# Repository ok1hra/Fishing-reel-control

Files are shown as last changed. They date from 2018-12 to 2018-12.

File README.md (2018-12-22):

# Fishing-reel-control 

KiCad PCB layout
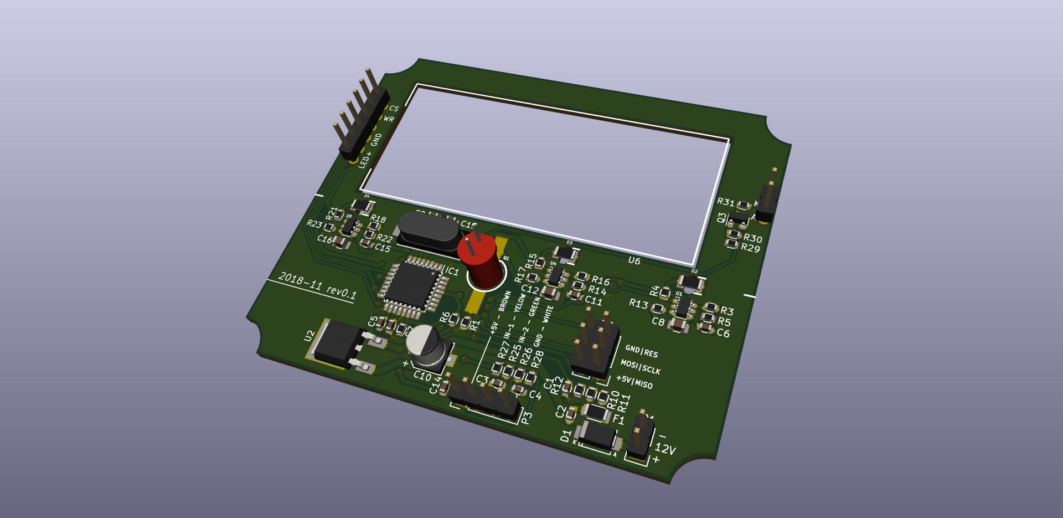
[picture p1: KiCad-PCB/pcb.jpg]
PCB


* [Schematics](KiCad-PCB/Ali-FM.pdf)
* [Interactive bom!](http://htmlpreview.github.io/?https://github.com/ok1hra/Fishing-reel-control/blob/master/KiCad-PCB/ibom.html)
* [STEP 3D model of PCB](KiCad-PCB/Ali-FM.step)
* [Firmware](https://github.com/ok1hra/Fishing-reel-control/tree/master/Arduino_firmware)

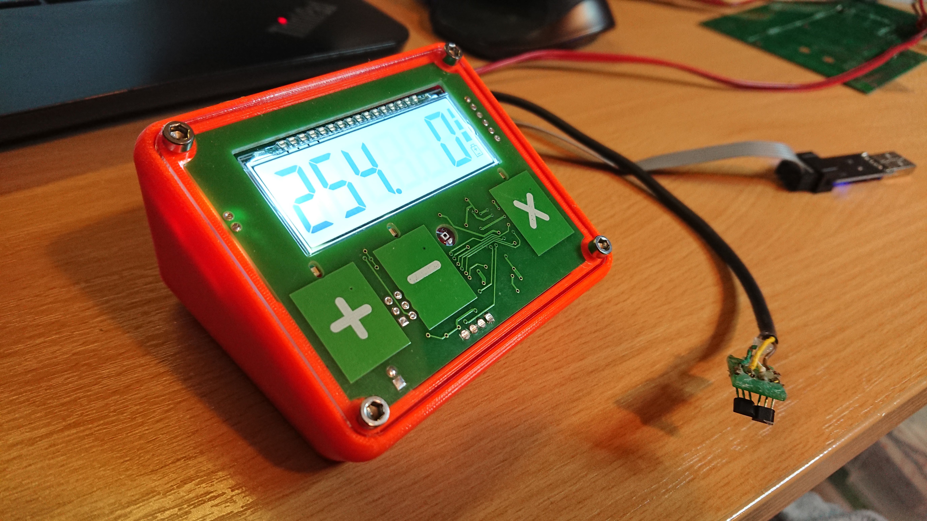
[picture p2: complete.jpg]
Complete


## Functionality
* Show battery voltage at start up
* LCD show counter, speed in metre unit + battery voltage bargraph
* Capacitive button sensor for up, down an reset with LED light feedback
* Ambient light sensor automaticaly adjust LCD backlight
* After 20 seconds storage last value, for recovery after restart power
* 12V DC power input
* Counter input for two hall effect switch
* Waterproof 3D printed case (PET)

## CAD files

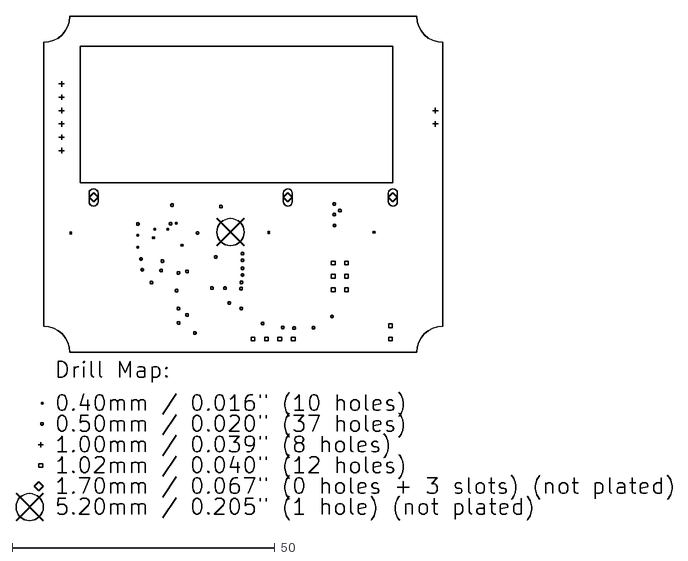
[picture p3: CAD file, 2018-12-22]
KiCad-PCB/gerber/Ali-FM-drl_map.dxf
124.9 x 96.1

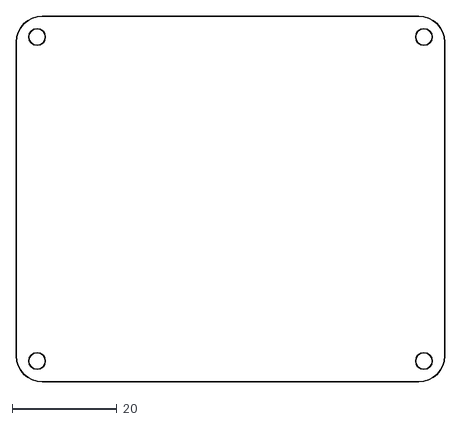
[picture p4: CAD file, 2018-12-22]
OpenScad-3Dmodel/plexi.dxf
82.0 x 70.0

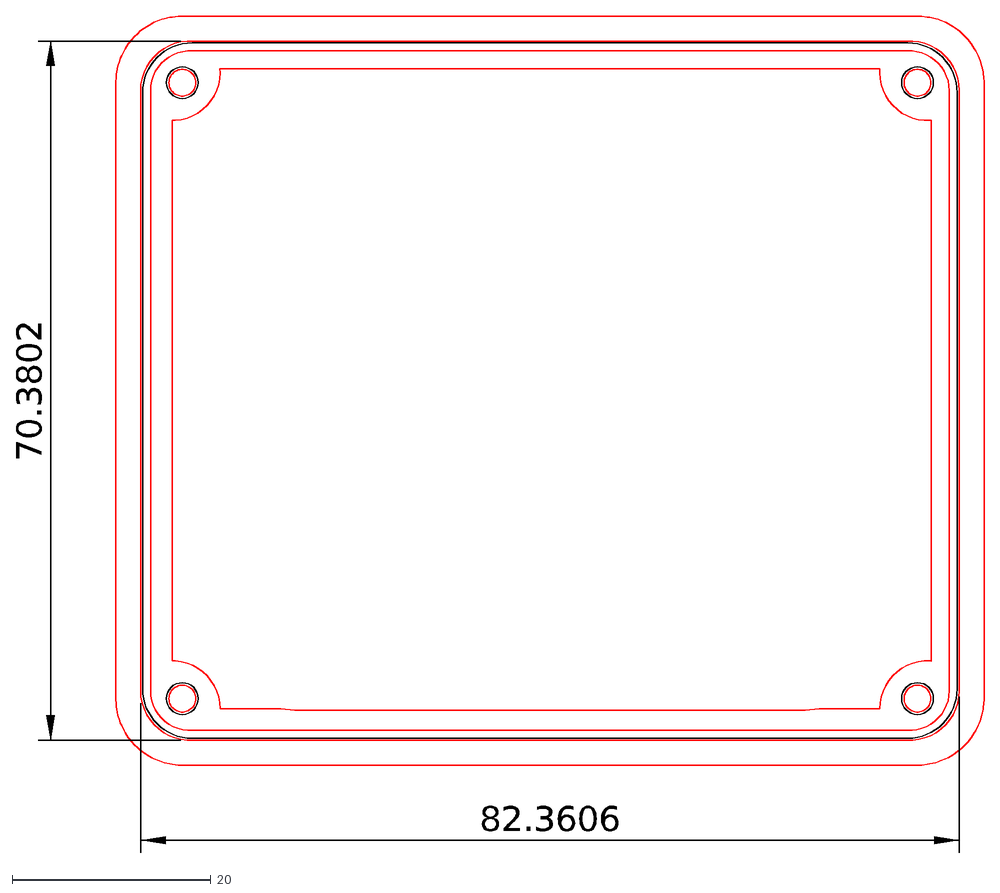
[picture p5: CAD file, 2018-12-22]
OpenScad-3Dmodel/ali-cut.dxf
70.3802
82.3606

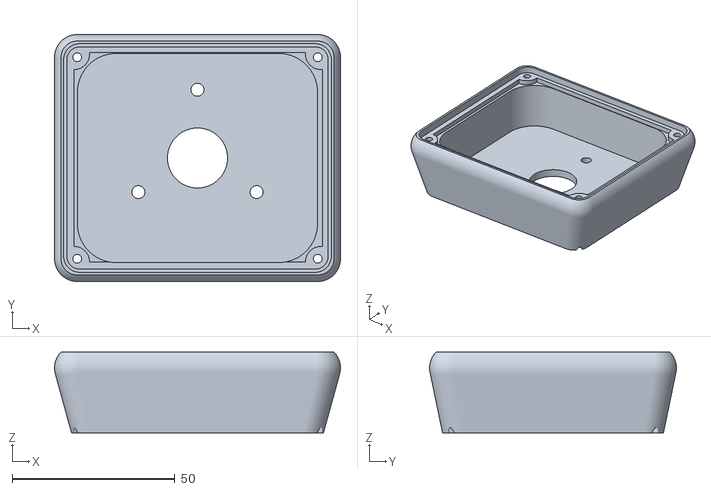
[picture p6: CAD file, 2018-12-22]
OpenScad-3Dmodel/ali.stl
88.0 x 76.0 x 24.9

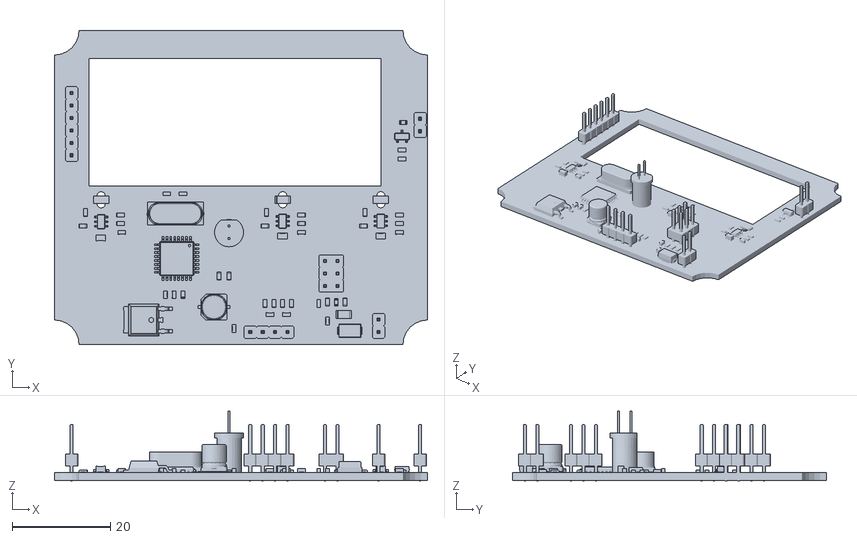
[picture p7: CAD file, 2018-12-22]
OpenScad-3Dmodel/Ali-FM.stl
76.0 x 64.0 x 14.2

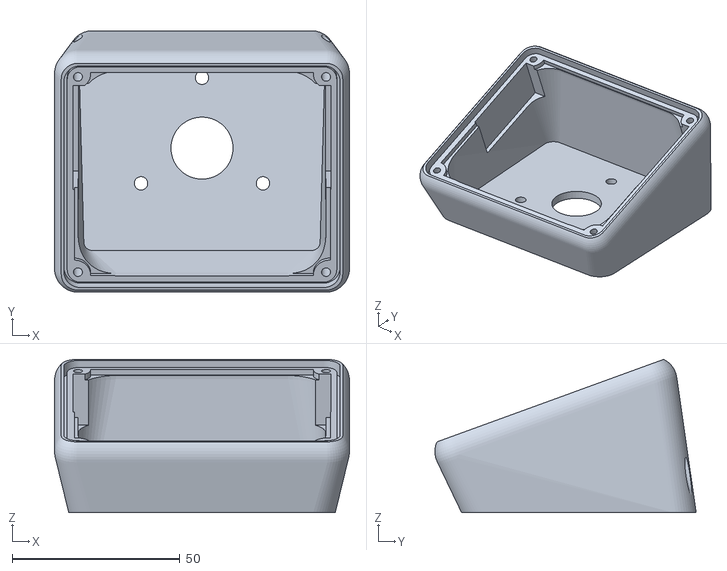
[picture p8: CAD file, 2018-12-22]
OpenScad-3Dmodel/ali2.stl
88.0 x 77.9 x 45.7

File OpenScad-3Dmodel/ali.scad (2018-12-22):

$fn=50;


%translate([0,0,10]) rotate([20,0,0]) translate([76/2,-64/2,23]) rotate([0,180,0]) import("Ali-FM.stl", convexity=3);

//            (xx,  yy, zz, rr, rrr, wall, screw){
// MountBoxFlat(77.5, 68, 20, 6,  7,   3,     2.7);

difference(){
    hull(){
        translate([0,0,10]) rotate([20,0,0]) OutTOP(77.5, 68, 20, 6,  7,   3,   0,  0.1);
        OutBOT(77.5, 68, 20, 6,  7,   3,  0, 0.1);
    }
    translate([0,0,10]) rotate([20,0,0]) InTOP(77.5, 68, 20, 6,  7,   3,     2.7);
    InFill(77.5, 68, 20, 6,  7,   3,     2.7);
    InBOT(77.5, 68, 20, 6,  7,   3,     2.7);
}



// 76x64mm

// CUT - F6 - Exportovat jako DXF
//projection(cut = true) translate([0,0,-22]) MountBoxBot(77.5, 68, 20, 6,  7,   3,  2.7);

module InFill(xx, yy, zz, rr, rrr, wall, screw, zzz){
    translate([0,0,5]) rotate([20,0,0])
    translate([0,13.5,20]) cube([77,33,17], center=true);
    hull(){
        translate([0,0,10]) rotate([20,0,0]) hull(){

            translate([-xx/2+2.3*rr, -yy/2+2.3*rr, 20]) cylinder(h=5, r=2*rr, center=false);
            translate([xx/2-2.3*rr, -yy/2+2.3*rr, 20]) cylinder(h=5, r=2*rr, center=false);
            translate([-xx/2+2.3*rr, yy/2-2.3*rr, 20]) cylinder(h=5, r=2*rr, center=false);
            translate([xx/2-2.3*rr, yy/2-2.3*rr, 20]) cylinder(h=5, r=2*rr, center=false);
        }
        translate([-xx/2+rr, -yy/2+rr, wall]) cylinder(h=0.1, r=rrr-wall-1.5, center=false);
        translate([xx/2-rr, -yy/2+rr, wall]) cylinder(h=0.1, r=rrr-wall-1.5, center=false);
        translate([-xx/2+rr, yy/2-rr, wall]) cylinder(h=0.1, r=rrr-wall, center=false);
        translate([xx/2-rr, yy/2-rr, wall]) cylinder(h=0.1, r=rrr-wall, center=false);
    }
}

module InTOP(xx, yy, zz, rr, rrr, wall, screw, zzz){
        // SCREW IN
        translate([-76/2+1, -64/2+1, -10]) cylinder(h=zz+20, d=screw, center=false);
        translate([76/2-1, -64/2+1, -10]) cylinder(h=zz+20, d=screw, center=false);
        translate([-76/2+1, 64/2-1, -20]) cylinder(h=zz+30, d=screw, center=false);
        translate([76/2-1, 64/2-1, -20]) cylinder(h=zz+30, d=screw, center=false);
        //PCB
        translate([-76/2, -64/2, zz+rrr-5.8]) PCB();
        // Top Cut
        translate([0, 0, zz+rrr-4]) Plexi(82.4, 70.4, 2, 5);
        translate([-xx, -yy, zz+rrr-2.1]) cube([xx*2, yy*2, zz]);
        translate([0, 0, zz+rrr-4-2]) Silicone(82.4, 70.4, 4, 5);
}
module OutTOP(xx, yy, zz, rr, rrr, wall, screw, zzz){
   hull(){
            translate([-76/2+1, -64/2+1, zz]) sphere(r=rrr, center=false);
            translate([76/2-1, -64/2+1, zz]) sphere(r=rrr, center=false);
            translate([-76/2+1, 64/2-1, zz]) sphere(r=rrr, center=false);
            translate([76/2-1, 64/2-1, zz]) sphere(r=rrr, center=false);
    }
}


module InBOT(xx, yy, zz, rr, rrr, wall, screw, zzz){
//    difference(){
//        union(){
//            // OUT BOT
//            hull(){
//                translate([-xx/2+rr, -yy/2+rr, 0]) cylinder(h=wall, r=rr, center=false);
//                translate([xx/2-rr, -yy/2+rr, 0]) cylinder(h=wall, r=rr, center=false);
//                translate([-xx/2+rr, yy/2-rr, 0]) cylinder(h=wall, r=rr, center=false);
//                translate([xx/2-rr, yy/2-rr, 0]) cylinder(h=wall, r=rr, center=false);
//            }
//        }
        // RING
        difference(){
            translate([0,0,-1]) cylinder(h=3.2, d=54, center=false);
            translate([0,0,-1]) cylinder(h=3.2, d=48, center=false);
        }
        // CENTER HOLE
        translate([0,0,-1]) cylinder(h=20, d=18.5, center=false);
        // MOUNT HOLE
        for(i = [90:120:360]){
            rotate([0,0,i]) translate([21,0,-1]) cylinder(h=20, d=4, center=false);
        }
//    }
}

module OutBOT(xx, yy, zz, rr, rrr, wall, screw, zzz){
    hull(){
        translate([-xx/2+rr, -yy/2+rr, 0]) cylinder(h=zzz, r=rrr, center=false);
        translate([xx/2-rr, -yy/2+rr, 0]) cylinder(h=zzz, r=rrr, center=false);
        translate([-xx/2+rr, yy/2-rr, 0]) cylinder(h=zzz, r=rrr, center=false);
        translate([xx/2-rr, yy/2-rr, 0]) cylinder(h=zzz, r=rrr, center=false);
    }
}
module MountBoxFlat(xx, yy, zz, rr, rrr, wall, screw, zzz){
    difference(){
        union(){
            difference(){
                union(){
                    // OUT BOT
                    hull(){
                        translate([-xx/2+rr, -yy/2+rr, 0]) cylinder(h=1, r=rr, center=false);
                            translate([-76/2+1, -64/2+1, zz]) sphere(r=rrr, center=false);
                        translate([xx/2-rr, -yy/2+rr, 0]) cylinder(h=1, r=rr, center=false);
                            translate([76/2-1, -64/2+1, zz]) sphere(r=rrr, center=false);
                        translate([-xx/2+rr, yy/2-rr, 0]) cylinder(h=1, r=rr, center=false);
                            translate([-76/2+1, 64/2-1, zz]) sphere(r=rrr, center=false);
                        translate([xx/2-rr, yy/2-rr, 0]) cylinder(h=1, r=rr, center=false);
                            translate([76/2-1, 64/2-1, zz]) sphere(r=rrr, center=false);
                    }
                }
                // IN
                hull(){
                    translate([-xx/2+2.3*rr, -yy/2+2.3*rr, wall]) cylinder(h=zz+20, r=2*rr, center=false);
                    translate([xx/2-2.3*rr, -yy/2+2.3*rr, wall]) cylinder(h=zz+20, r=2*rr, center=false);
                    translate([-xx/2+2.3*rr, yy/2-2.3*rr, wall]) cylinder(h=zz+20, r=2*rr, center=false);
                    translate([xx/2-2.3*rr, yy/2-2.3*rr, wall]) cylinder(h=zz+20, r=2*rr, center=false);
                }
                // RING
                difference(){
                    translate([0,0,-1]) cylinder(h=3.2, d=54, center=false);
                    translate([0,0,-1]) cylinder(h=3.2, d=48, center=false);
                }
                // CENTER HOLE
                translate([0,0,-1]) cylinder(h=wall+2, d=18.5, center=false);
                // MOUNT HOLE
                for(i = [90:120:360]){
                    rotate([0,0,i]) translate([21,0,-1]) cylinder(h=wall+2, d=4, center=false);
                }
            }
        }
        // SCREW IN
        translate([-76/2+1, -64/2+1, -1]) cylinder(h=zz+20, d=screw, center=false);
        translate([76/2-1, -64/2+1, -1]) cylinder(h=zz+20, d=screw, center=false);
        translate([-76/2+1, 64/2-1, -1]) cylinder(h=zz+20, d=screw, center=false);
        translate([76/2-1, 64/2-1, -1]) cylinder(h=zz+20, d=screw, center=false);
        //PCB
        translate([-76/2, -64/2, zz+rrr-5.8]) PCB();
        // Top Cut
        translate([0, 0, zz+rrr-4]) Plexi(82.4, 70.4, 2, 5);
        translate([-xx, -yy, zz+rrr-2.1]) cube([xx*2, yy*2, zz]);
        translate([0, 0, zz+rrr-4-2]) Silicone(82.4, 70.4, 4, 5);

//        translate([-xx, -yy, -1]) cube([xx*2, yy*2, 10]);

        
    }    
}



module Silicone(xx, yy, zz, rr){
    difference(){
        hull(){
            translate([-xx/2+rr, -yy/2+rr, 0]) cylinder(h=zz, r=rr, center=false);
            translate([xx/2-rr, -yy/2+rr, 0]) cylinder(h=zz, r=rr, center=false);
            translate([-xx/2+rr, yy/2-rr, 0]) cylinder(h=zz, r=rr, center=false);
            translate([xx/2-rr, yy/2-rr, 0]) cylinder(h=zz, r=rr, center=false);
        }    
        hull(){
            translate([-xx/2+rr, -yy/2+rr, -1]) cylinder(h=zz+2, r=rr-1, center=false);
            translate([xx/2-rr, -yy/2+rr, -1]) cylinder(h=zz+2, r=rr-1, center=false);
            translate([-xx/2+rr, yy/2-rr, -1]) cylinder(h=zz+2, r=rr-1, center=false);
            translate([xx/2-rr, yy/2-rr, -1]) cylinder(h=zz+2, r=rr-1, center=false);
        }    
    }
}



module Plexi(xx, yy, zz, rr){
    hull(){
        translate([-xx/2+rr, -yy/2+rr, 0]) cylinder(h=zz, r=rr, center=false);
        translate([xx/2-rr, -yy/2+rr, 0]) cylinder(h=zz, r=rr, center=false);
        translate([-xx/2+rr, yy/2-rr, 0]) cylinder(h=zz, r=rr, center=false);
        translate([xx/2-rr, yy/2-rr, 0]) cylinder(h=zz, r=rr, center=false);
    }    
}

module PCB(){
        difference(){
        translate([0,0,0]) cube([76.4, 64.4, 2]);
        translate([0,0,-1]) cylinder(h=4, r=4.8, center=false);
        translate([76,0,-1]) cylinder(h=4, r=4.8, center=false);
        translate([76,64,-1]) cylinder(h=4, r=4.8, center=false);
        translate([0,64,-1]) cylinder(h=4, r=4.8, center=false);
    }
}
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

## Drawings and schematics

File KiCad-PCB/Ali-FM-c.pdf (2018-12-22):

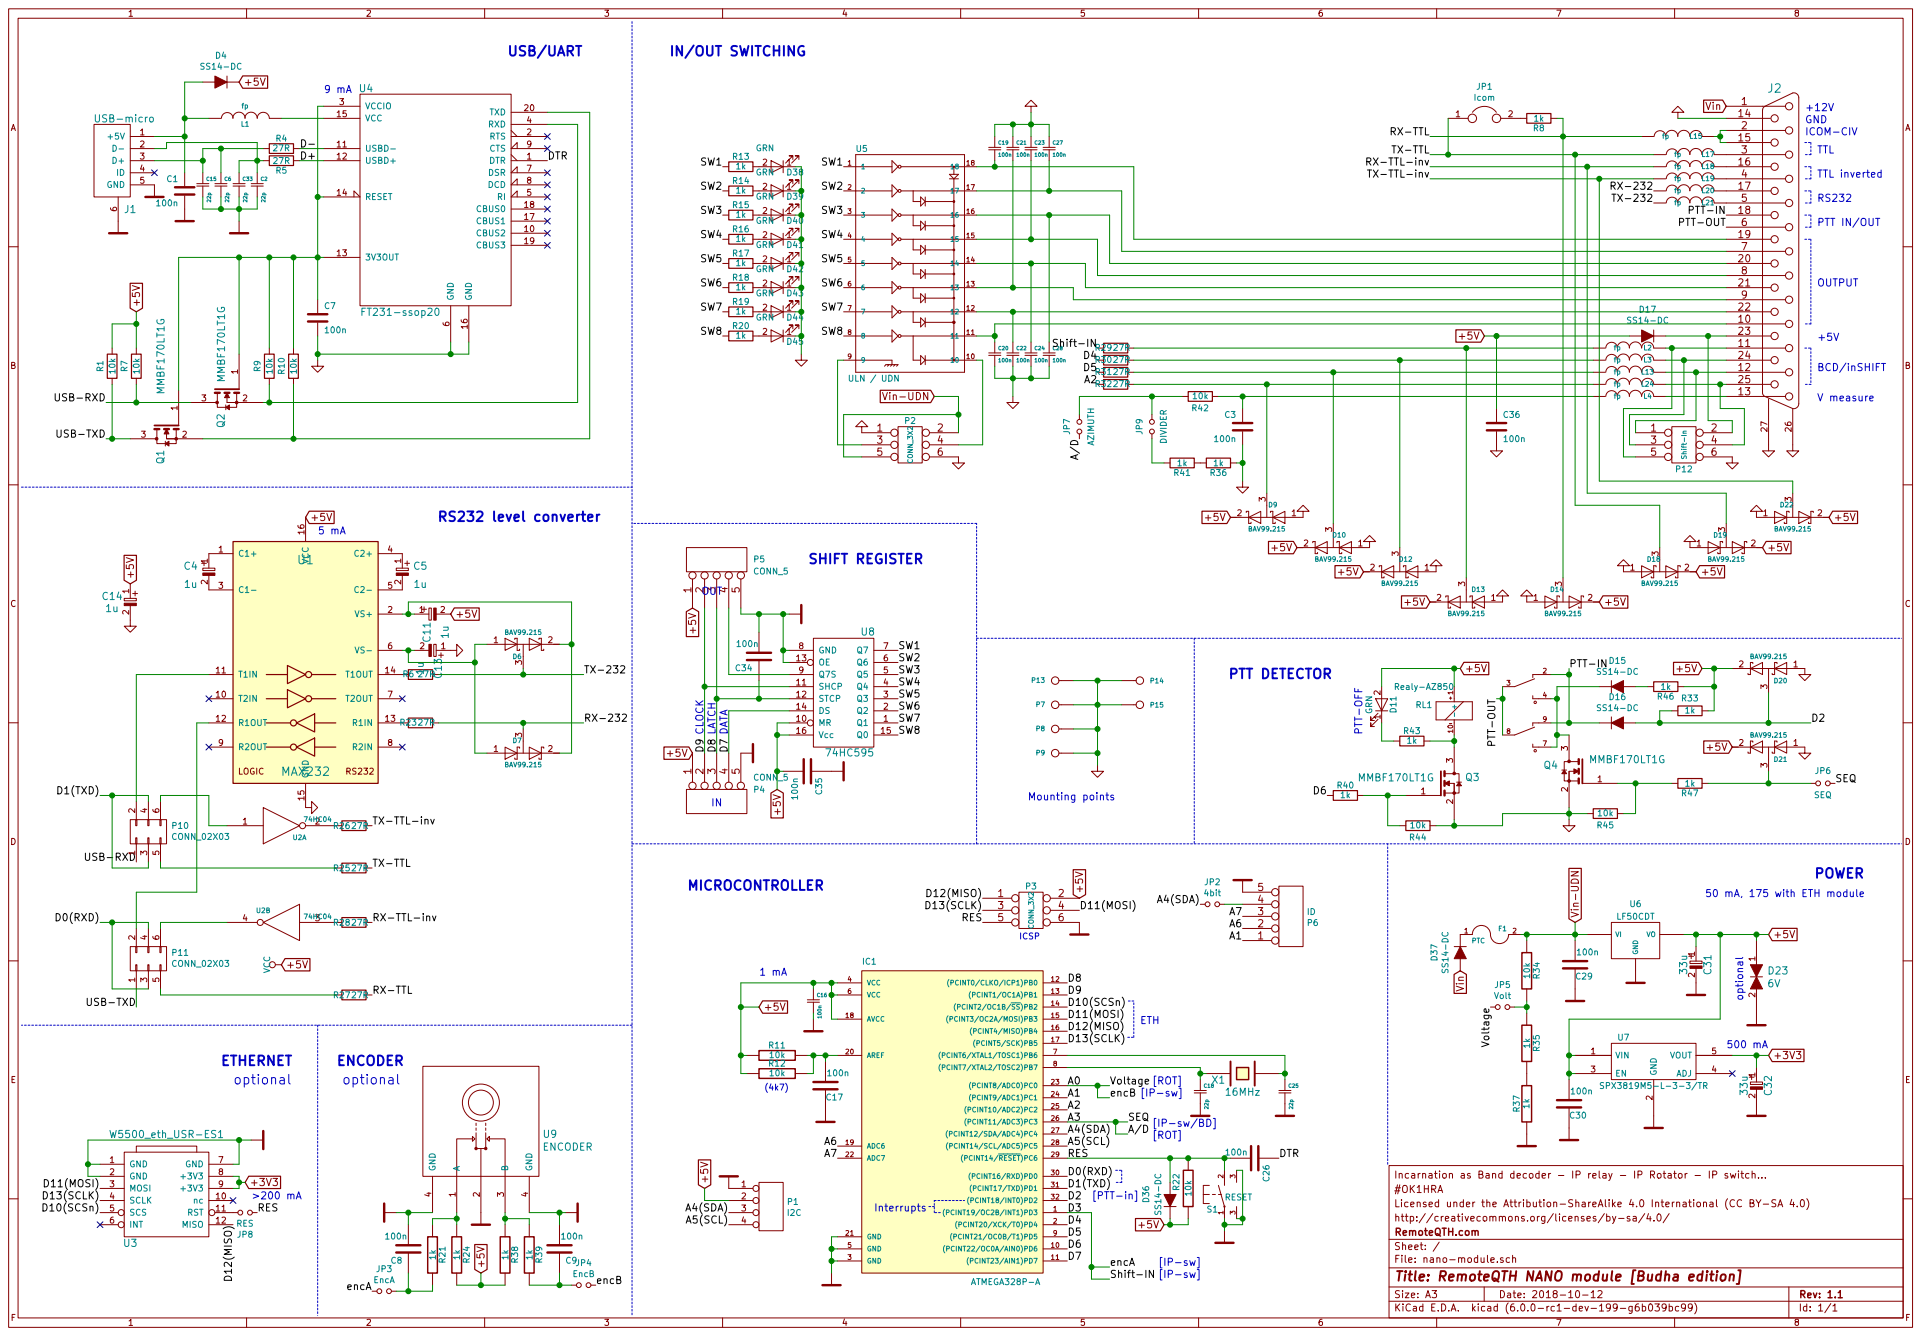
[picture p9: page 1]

6 DSR 7 DCD 8 CTS 9 CBUS2 10 TXD 20 USBD- 11 USBD+ 12

50 mA, 175 with ETH module

Incarnation as Band decoder - IP relay - IP Rotator - IP switch...
Licensed under the Attribution-ShareAlike 4.0 International (CC BY-SA 4.0) #OK1HRA

http://creativecommons.org/licenses/by-sa/4.0/
Id: 1/1 Title: RemoteQTH NANO module [Budha edition] File: nano-module.sch Sheet: / RemoteQTH.com

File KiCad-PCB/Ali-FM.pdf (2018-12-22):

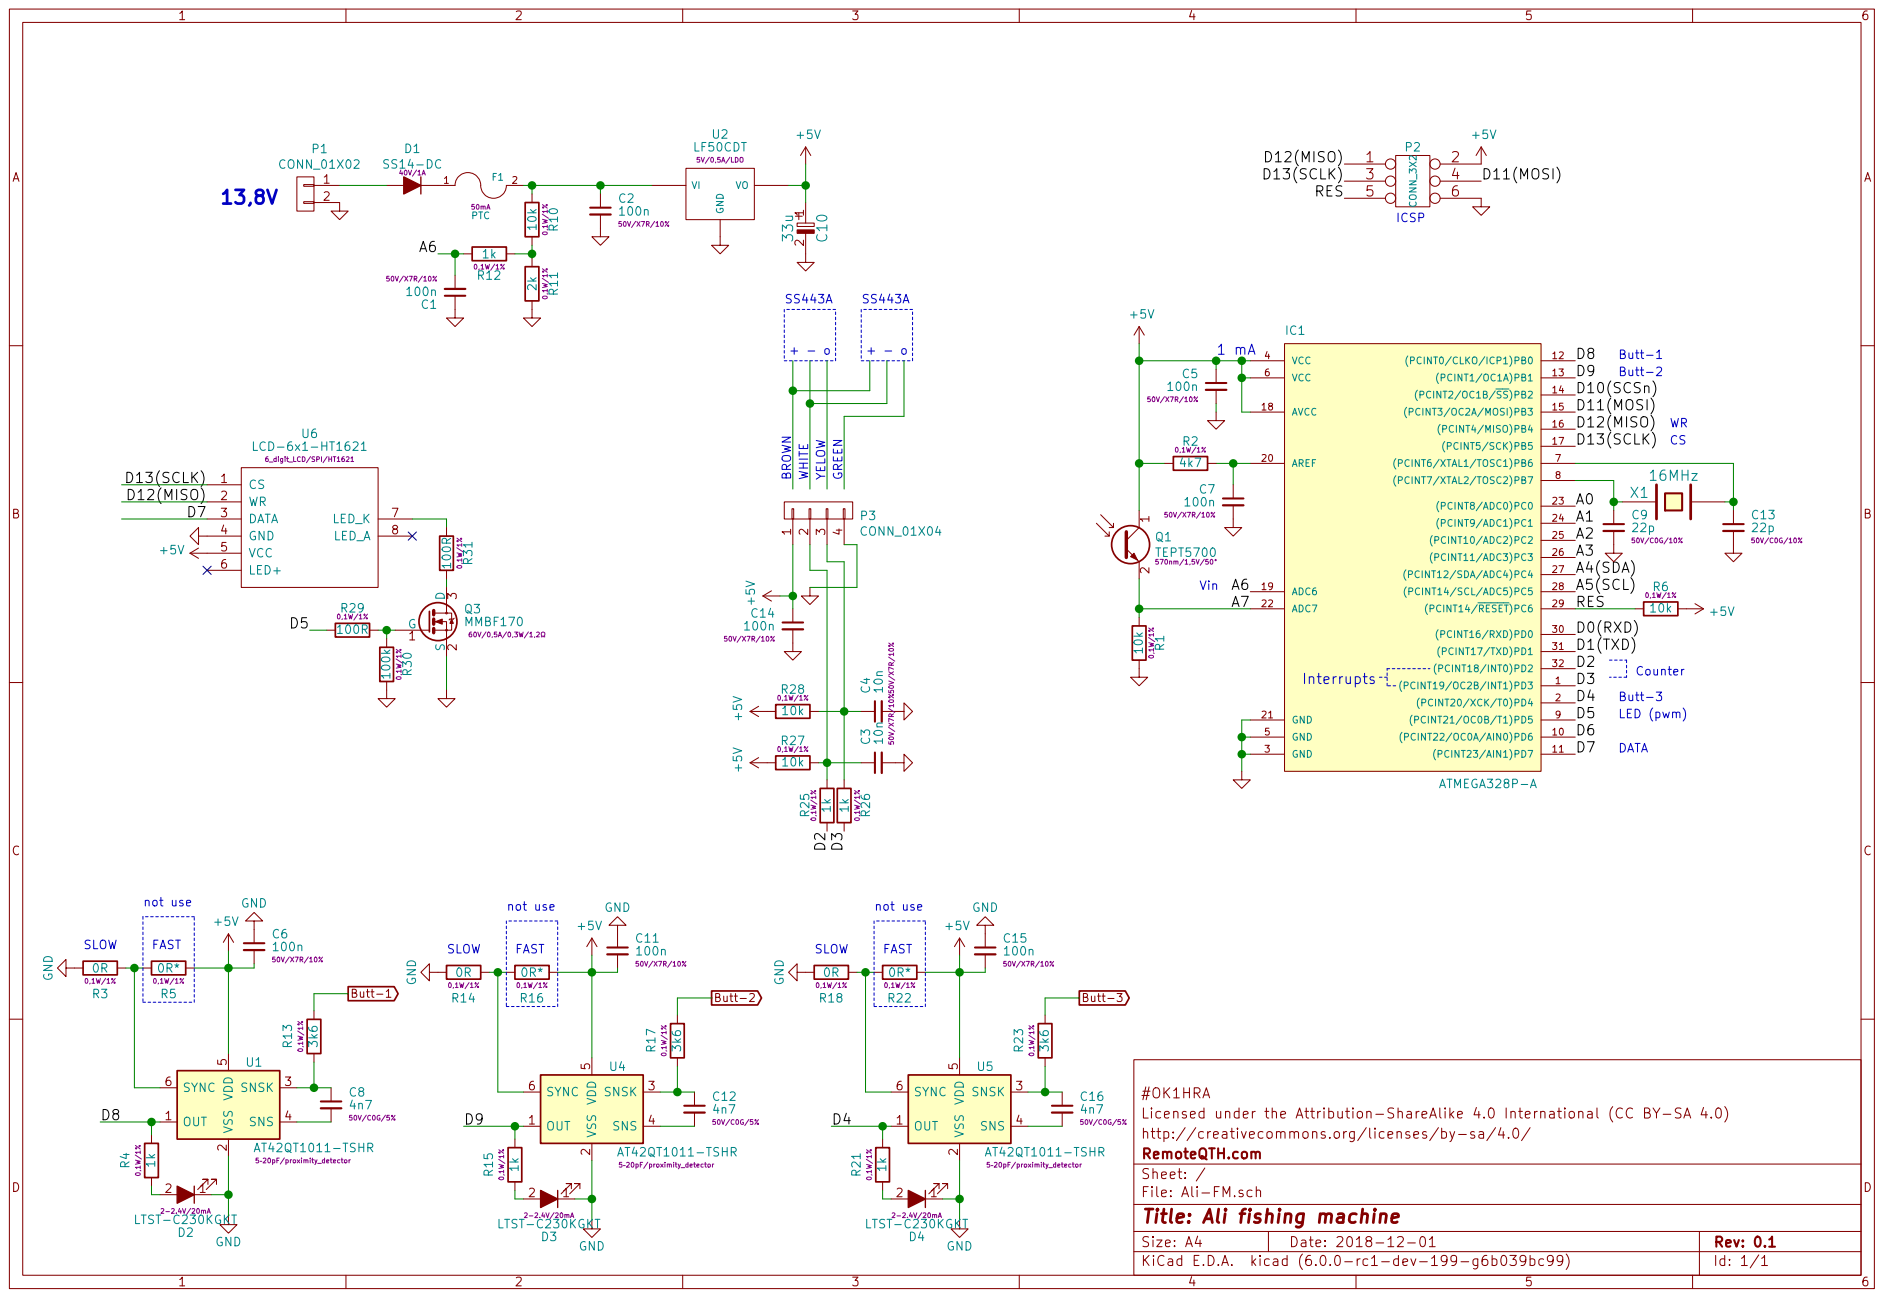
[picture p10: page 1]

Licensed under the Attribution-ShareAlike 4.0 International (CC BY-SA 4.0) #OK1HRA

http://creativecommons.org/licenses/by-sa/4.0/
File: Ali-FM.sch Sheet: / RemoteQTH.com

Id: 1/1 Title: Ali fishing machine

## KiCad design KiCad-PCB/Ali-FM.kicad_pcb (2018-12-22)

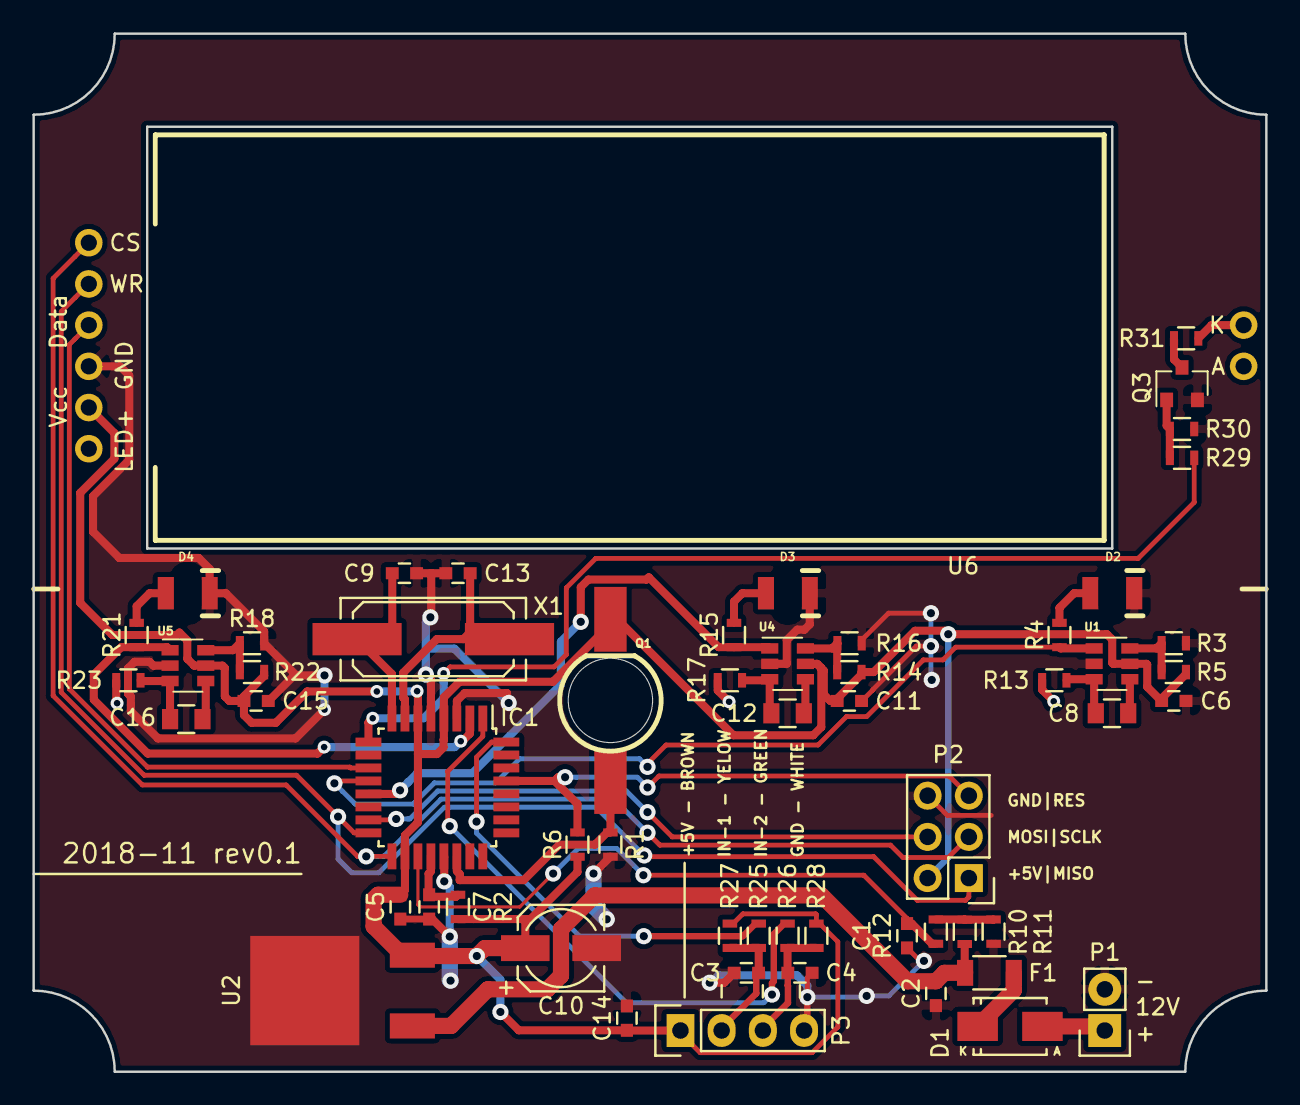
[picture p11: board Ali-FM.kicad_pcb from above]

Board: 2 copper layers, 76.0 x 64.0 mm, 58 parts (0 on the bottom side), 39 nets.

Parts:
C1, C2, C5, C6, C7, C11, C14, C15: 100n; C_0603
C3, C4: 10n; C_0603
C8, C12, C16: 4n7; C_0805
C9, C13: 22p; C_0603
C10: 33u; c_elec_5x5.7
D1: SS14-DC; SMA_Standard
D2, D3, D4: LTST-C230KGKT; LED-1206-invert-mount
F1: PTC; C_1206
IC1: ATMEGA328P-A; TQFP-32_7x7mm_Pitch0.8mm
P1: CONN_01X02; Pin_Header_Straight_1x02
P2: CONN_3X2; Pin_Header_Straight_2x03
P3: CONN_01X04; Pin_Header_Straight_1x04
Q1: TEPT5700; PhotoTransistor-inPCB
Q3: MMBF170; SOT-23
R1, R6, R10, R27, R28: 10k; R_0603
R2: 4k7; R_0603
R3, R14, R18: 0R; R_0603
R4, R12, R15, R21, R25, R26: 1k; R_0603
R5, R16, R22: 0R*; R_0603
R11: 2k; R_0603
R13, R17, R23: 3k6; R_0603
R29, R31: 100R; R_0603
R30: 100k; R_0603
U1, U4, U5: AT42QT1011-TSHR; SOT-23-6
U2: LF50CDT; D-Pak_TO252AA
U6: LCD-6x1-HT1621
X1: 16MHz; Q_49U3HMS

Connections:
+5V: C5.1, C6.2, C10.1, C11.2, C14.1, C15.2, IC1.4, IC1.6, IC1.18, P2.2, P3.1, Q1.1, R2.2, R5.2, R6.1, R16.2, R22.2, R27.2, R28.2, U1.5, U2.3, U4.5, U5.5, U6.5
/A6: C1.2, IC1.19, R12.1
/A7: IC1.22, Q1.2, R1.1
/D2: IC1.32, R25.2
/D3: IC1.1, R26.2
/D4: IC1.2, R21.2, U5.1
/D5: IC1.9, R29.2
/D7: IC1.11, U6.3
/D8: IC1.12, R4.2, U1.1
/D9: IC1.13, R15.2, U4.1
/D11(MOSI): IC1.15, P2.4
/D12(MISO): IC1.16, P2.1, U6.2
/D13(SCLK): IC1.17, P2.3, U6.1
/RES: IC1.29, P2.5, R6.2
GND: C1.1, C2.2, C3.2, C4.2, C5.2, C6.1, C7.2, C9.2, C10.2, C11.1, C13.2, C14.2, C15.1, D2.1, D3.1, D4.1, IC1.3, IC1.5, IC1.21, P1.2, P2.6, P3.4, Q3.2, R1.2, R3.1, R11.1, R14.1, R18.1, R30.2, U1.2, U2.4, U4.2, U5.2, U6.4
unnamed: C2.1, F1.2, R10.2, U2.1
unnamed: C3.1, P3.2, R25.1, R27.1
unnamed: C4.1, P3.3, R26.1, R28.1
unnamed: C7.1, IC1.20, R2.1
unnamed: C8.1, R13.2, U1.3
unnamed: C8.2, U1.4
unnamed: C9.1, IC1.8, X1.1
unnamed: C12.1, R17.2, U4.3
unnamed: C12.2, U4.4
unnamed: C13.1, IC1.7, X1.2
unnamed: C16.1, R23.2, U5.3
unnamed: C16.2, U5.4
unnamed: D1.1, F1.1
unnamed: D1.2, P1.1
unnamed: D2.2, R4.1
unnamed: D3.2, R15.1
unnamed: D4.2, R21.1
unnamed: Q3.1, R29.1, R30.1
unnamed: Q3.3, R31.1
unnamed: R3.2, R5.1, U1.6
unnamed: R10.1, R11.2, R12.2
unnamed: R14.2, R16.1, U4.6
unnamed: R18.2, R22.1, U5.6
unnamed: R31.2, U6.7

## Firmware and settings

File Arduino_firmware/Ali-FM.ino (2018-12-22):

#include <EEPROM.h>
/*
avrdude -P usb -b 19200 -c usbasp -p atmega328p -U flash:w:/home/dan/Arduino/hra/ok1hra/Ali-FM/Ali-FM.ino.with_bootloader.eightanaloginputs.hex -U efuse:w:0xFD:m -U hfuse:w:0xDA:m -U lfuse:w:0xFF:m


winch diameter 20cm = 0,628 m perimeter
*/

//===================================================
const float CountRawLong                  = 0.628;  // meter
int SecondAfterLastChangeStorageToEeprom  = 20;    // second
//===================================================

// #define DEBUG_ON_IPSW
float BattLevel[3]={12.2, 12.4, 12.7};  // 50% 75% 100%
byte BattLevelResult[3]={0,0,0};
bool BattLevelResultZeroFlash;
float ArefVoltage = 4.427;            // Measure on Aref pin 20 for calibrate
float VoltageDrop = 1.1;              // drop on diode and fuse
float Divider = 6;                    // voltage divider
int CounterRaw = 0;
float Counter = 0;
int CounterForEeprom = 0;
float CounterPrev = 0;
float Speed = 0;
long ButtReactTime[2]{0,200};
long SpeedTime[2]{0,1000};
long SlowRefreshTime[2]{0,1000};
long EepromTime[2]{0,SecondAfterLastChangeStorageToEeprom*1000};
bool EepromNeedChange=false;

const int CS  = 13;  //Pin 2 as chip selection output
const int WR  = 12;  //Pin 3 as read clock output
const int DATA= 7;  //Pin 4 as Serial data output
const int BACK_LIGHT = 5;
const int VoltagePin = A6;
const int PlusButtonPin = 8;
const int MinusButtonPin = 9;
const int StopButtonPin = 4;
const int LIGHT = A7;
#if defined(DEBUG_ON_IPSW)
  const int EncPinA = 3;
  const int EncPinB = A0;
#else
  const int EncPinA = 2;
  const int EncPinB = 3;
#endif

#define CS1    digitalWrite(CS, HIGH)
#define CS0    digitalWrite(CS, LOW)
#define WR1    digitalWrite(WR, HIGH)
#define WR0    digitalWrite(WR, LOW)
#define DATA1  digitalWrite(DATA, HIGH)
#define DATA0  digitalWrite(DATA, LOW)

#define sbi(x, y)  (x |= (1 << y))
#define cbi(x, y)  (x &= ~(1 <<y ))
#define uchar   unsigned char
#define uint   unsigned int

#define  ComMode    0x52
#define  RCosc      0x30
#define  LCD_on     0x06
#define  LCD_off    0x04
#define  Sys_en     0x02
#define  CTRl_cmd   0x80
#define  Data_cmd   0xa0

/*0,1,2,3,4,5,6,7,8,9,A,b,C,c,d,E,F,H,h,L,n,N,o,P,r,t,U,- (26), (27),degree (28),comma */
const char num[]={0x7D,0x60,0x3E,0x7A,0x63,0x5B,0x5F,0x70,0x7F,0x7B,0x77,0x4F,0x1D,0x0E,0x6E,0x1F,0x17,0x67,0x47,0x0D,0x46,0x75,0x37,0x06,0x0F,0x6D,0x02,0x00,0x33,0x80};
//char dispnum[6]={0x00,0x00,0x00,0x00,0x00,0x00};

int Digit[6];
bool LcdNeedRefresh = false;
long LcdRefresh[2]{0,500};

int ora, zora, uora;
int minut, zmin, umin;
int temperatura, temp, ztemp, utemp, stemp;
byte semn = 0;

//--------------------------------------------------------------------------------------------------------------
void setup() {
  #if defined(DEBUG_ON_IPSW)
    Serial.begin(115200);
  #endif
  analogReference(INTERNAL);
  Serial.begin(115200);
  Serial.println(" ");
  pinMode(CS, OUTPUT); //
  pinMode(WR, OUTPUT); //
  pinMode(DATA, OUTPUT); //
  pinMode(LIGHT, INPUT); //
  pinMode(BACK_LIGHT, OUTPUT); //
  analogWrite(BACK_LIGHT, 255);
  pinMode(EncPinA, INPUT_PULLUP); //
  pinMode(EncPinB, INPUT_PULLUP); //
  CS1;
  DATA1;
  WR1;
  delay(50);
  Init_1621();
  HT1621_all_on(16);
  // delay(500);
  // HT1621_all_off(16);
  LcdNeedRefresh=true;
  LcdShowAll((float(analogRead(VoltagePin)) * ArefVoltage * Divider / 1023.0 + VoltageDrop)*100);
  delay(2000);
  Counter=EEPROM.read(0)*100+EEPROM.read(1)*10+EEPROM.read(2);
  CounterForEeprom=int(Counter);
  CounterPrev=Counter;
  attachInterrupt(digitalPinToInterrupt(EncPinA), EncoderCount, FALLING);
  // detachInterrupt(digitalPinToInterrupt(EncPinA);
}
//--------------------------------------------------------------------------------------------------------------

void loop() {
  #if defined(DEBUG_ON_IPSW)
    // nil
  #else
  CounterSpeed();
  Buttons();


  if(millis()-ButtReactTime[0]<ButtReactTime[1]){
    LcdShow(int(Counter), 0);
  }else{
    LcdShow(int(Counter), abs(Speed));
  }

  float voltage = float(analogRead(VoltagePin)) * ArefVoltage * Divider / 1023.0 + VoltageDrop;
  if(millis()-SlowRefreshTime[0]>SlowRefreshTime[1]){
    Battery(voltage);

    // BackLight
    analogWrite(BACK_LIGHT, map(analogRead(LIGHT), 0, 1024, 255, 0) );

    // EEPROM
    if(CounterForEeprom!=int(Counter)){
      CounterForEeprom=int(Counter);
      EepromTime[0]=millis();
      EepromNeedChange=true;
    }
    if(millis()-EepromTime[0]>EepromTime[1] && EepromNeedChange==true){
      EepromNeedChange=false;
      EEPROM.write(0, Digit[0]);
      EEPROM.write(1, Digit[1]);
      EEPROM.write(2, Digit[2]);
      // analogWrite(BACK_LIGHT, 0);
    }
    SlowRefreshTime[0]=millis();
  }
  #endif
}

//---------------------------------------------------------------------------------------------------------
//---------------------------------------------------------------------------------------------------------
void EncoderCount(){    // interrupt
  // detachInterrupt(digitalPinToInterrupt(EncPinA));
  if(digitalRead(EncPinB)==0){
    CounterRaw++;
  }else{
    CounterRaw--;
  }

  if(CounterRaw>999){
    CounterRaw=999;
  }
  if(CounterRaw<0){
    CounterRaw=0;
  }
  Counter = CounterRaw*CountRawLong;

  #if defined(DEBUG_ON_IPSW)
    for (int i=0; i <= 20; i++){
    Counter=0.5*i;
    CounterRaw=Counter*CountRawLong;
      Serial.print("CounterRaw ");
      Serial.print(CounterRaw);
      Serial.print(" = CountRawLong ");
      Serial.print(CountRawLong);
      Serial.print(" * Counter ");
      Serial.println(Counter);
    }
  #endif

  LcdNeedRefresh=true;
  // attachInterrupt(digitalPinToInterrupt(EncPinA), EncoderCount, FALLING);
}

//---------------------------------------------------------------------------------------------------------
void Battery(float voltage){

  if(voltage>BattLevel[2]){
    // 100%
    BattLevelResult[2]=0x80;
    BattLevelResult[1]=0x80;
    BattLevelResult[0]=0x80;
  }else if(voltage>BattLevel[1] && voltage<=BattLevel[2]){
    // 75%
    BattLevelResult[2]=0x00;
    BattLevelResult[1]=0x80;
    BattLevelResult[0]=0x80;
  }else if(voltage>BattLevel[0] && voltage<=BattLevel[1]){
    // 50%
    BattLevelResult[2]=0x00;
    BattLevelResult[1]=0x00;
    BattLevelResult[0]=0x80;
  }else if(voltage<=BattLevel[0]){
    // <50%
    BattLevelResult[2]=0x00;
    BattLevelResult[1]=0x00;
    BattLevelResult[0]=0x00;
  }
}

//---------------------------------------------------------------------------------------------------------

void CounterSpeed(){
  if(millis()-SpeedTime[0]>SpeedTime[1]){
    Speed=Counter-CounterPrev;
    CounterPrev=Counter;
    if(Speed>99){
      Speed=99;
    }
    if(Speed<-99){
      Speed=-99;
    }
    SpeedTime[0]=millis();
  }
}
//---------------------------------------------------------------------------------------------------------
void Buttons(){
  if(millis()-ButtReactTime[0]>ButtReactTime[1]){
    byte Plus = digitalRead(PlusButtonPin);
    byte Minus = digitalRead(MinusButtonPin);
    byte Stop = digitalRead(StopButtonPin);

    if(Plus==1 && Minus==0 && Stop==0){
      if(abs(Speed)>=3){
        Counter+=10;
      }else{
        Counter++;
      }
      if(Counter>999){Counter=999;}
      ButtReactTime[0]=millis();
      LcdNeedRefresh=true;
    }
    if(Plus==0 && Minus==1 && Stop==0){
      if(abs(Speed)>=3){
        Counter-=10;
      }else{
        Counter--;
      }
      if(Counter<0){Counter=0;}
      ButtReactTime[0]=millis();
      LcdNeedRefresh=true;
    }
    if(Plus==0 && Minus==0 && Stop==1){
      Counter=0;
      LcdNeedRefresh=true;
    }
    if(Plus==1 || Minus==1 || Stop==1){
      CounterRaw=Counter/CountRawLong;
    }
    Plus=0;
    Minus=0;
    Stop=0;
    ButtReactTime[0]=millis();
  }
}
//---------------------------------------------------------------------------------------------------------

void LcdShow(int LeftNumberToShow, int RightNumberToShow){
  if(millis()-LcdRefresh[0]>LcdRefresh[1] || LcdNeedRefresh == true){
    // split
    SplitNumberToDigit(LeftNumberToShow, 1);
    SplitNumberToDigit(RightNumberToShow, 0);
    HT1621_all_off(16);

    // RIGHT
    Write_1621(0,num[Digit[5]]);

    if(Digit[4]==0 && Digit[3]==0){
      if(Speed<0 && millis()-ButtReactTime[0]>ButtReactTime[1]){
        Write_1621(2,num[26]); // Negative sign
      }else{
        Write_1621(2,0x00);
      }
    }else{
      Write_1621(2,num[Digit[4]]);
    }

    if(Digit[3]==0){
      if(Speed<0 && Digit[4]!=0 && millis()-ButtReactTime[0]>ButtReactTime[1]){
        Write_1621(4,num[26]+num[29]); // Negative sign
      }else{
        Write_1621(4,0x00+num[29]);   // blank + dot
      }
    }else{
      Write_1621(4,num[Digit[3]]+num[29]);
    }


    // LEFT
    byte FLASH=0x00;
    if(BattLevelResult[0]==0){
      BattLevelResultZeroFlash= !BattLevelResultZeroFlash;
    }
    if(BattLevelResultZeroFlash==true){
      FLASH=0x80;
    }

    Write_1621(6,num[Digit[2]]+BattLevelResult[0]+FLASH);

    if(Digit[1]==0 && Digit[0]==0){
      Write_1621(8,0x00+BattLevelResult[1]);
    }else{
      Write_1621(8,num[Digit[1]]+BattLevelResult[1]);
    }

    if(Digit[0]==0){
      Write_1621(10,0x00+BattLevelResult[2]);
    }else{
      Write_1621(10,num[Digit[0]]+BattLevelResult[2]);
    }

  // Write_1621(2,num[Digit[4]]);
  // Write_1621(4,num[Digit[3]]+num[29]);  // number with decimal points
  // Write_1621(6,num[Digit[2]]);
  // Write_1621(8,num[Digit[1]]);
  // Write_1621(10,num[Digit[0]]);
  LcdRefresh[0]=millis();
  LcdNeedRefresh = false;
  }
}
//---------------------------------------------------------------------------------------------------------

void LcdShowAll(long NumberToShow){
  if(millis()-LcdRefresh[0]>LcdRefresh[1] || LcdNeedRefresh == true){
    // split
    SplitNumberToAllDigit(NumberToShow);
    HT1621_all_off(16);

    Write_1621(0,num[Digit[5]]);

    Write_1621(2,num[Digit[4]]+num[29]);

    Write_1621(4,num[Digit[3]]);


    byte FLASH=0x00;
    if(BattLevelResult[0]==0){
      BattLevelResultZeroFlash= !BattLevelResultZeroFlash;
    }
    if(BattLevelResultZeroFlash==true){
      FLASH=0x80;
    }

    if(Digit[2]==0 && Digit[1]==0 && Digit[0]==0){
      Write_1621(6,0x00+BattLevelResult[0]+FLASH);
    }else{
      Write_1621(6,num[Digit[2]]+BattLevelResult[0]+FLASH);
    }

    if(Digit[1]==0 && Digit[0]==0){
      Write_1621(8,0x00+BattLevelResult[1]);
    }else{
      Write_1621(8,num[Digit[1]]+BattLevelResult[2]);
    }

    if(Digit[0]==0){
      Write_1621(10,0x00+BattLevelResult[2]);
    }else{
      Write_1621(10,num[Digit[0]]+BattLevelResult[2]);
    }

  // Write_1621(2,num[Digit[4]]);
  // Write_1621(4,num[Digit[3]]+num[29]);  // number with decimal points
  // Write_1621(6,num[Digit[2]]);
  // Write_1621(8,num[Digit[1]]);
  // Write_1621(10,num[Digit[0]]);
  LcdRefresh[0]=millis();
  LcdNeedRefresh = false;
  }
}
//---------------------------------------------------------------------------------------------------------

void SplitNumberToDigit(int NUMBER, bool LEFT){
  if(LEFT==false){
    Digit[5] = (NUMBER / 1) % 10;
    Digit[4] = (NUMBER / 10) % 10;
    Digit[3] = (NUMBER / 100) % 10;
    // Digit[2] = (NUMBER / 1000) % 10;
    // Digit[1] = (NUMBER / 10000) % 10;
    // Digit[0] = (NUMBER / 100000) % 10;
  }else{
    Digit[2] = (NUMBER / 1) % 10;
    Digit[1] = (NUMBER / 10) % 10;
    Digit[0] = (NUMBER / 100) % 10;
  }
}
//---------------------------------------------------------------------------------------------------------

void SplitNumberToAllDigit(long NUMBER){
    Digit[5] = (NUMBER / 1) % 10;
    Digit[4] = (NUMBER / 10) % 10;
    Digit[3] = (NUMBER / 100) % 10;
    Digit[2] = (NUMBER / 1000) % 10;
    Digit[1] = (NUMBER / 10000) % 10;
    Digit[0] = (NUMBER / 100000) % 10;
}
//---------------------------------------------------------------------------------------------------------
// http://arduinolearning.com/code/ht1621-6-digit-7-segment-display-example.php
// random clock and temperature with decimal point by Nicu FLORICA (niq_ro) - http://www.arduinotehniq.com
// ver.4 - Craiova, 14.10.2018

void DEMO(){
  ora = random(24);
  zora = ora/10;
  uora = ora%10;
Serial.print(ora);
Serial.print(" = ");
Serial.print(zora);
Serial.print(uora);
Serial.println(" ?");
  minut = random(60);
  zmin = minut/10;
  umin = minut%10;
Serial.print(minut);
Serial.print(" = ");
Serial.print(zmin);
Serial.print(umin);
Serial.println(" ?");

  temperatura = random(-390,390);
  if (temperatura < 0)
  {
    temp = - temperatura;
    semn = 2 ;  // negative
  }
else
   {
   temp = temperatura;
   semn = 0 ;  // negative
   }

   ztemp = temp/100;
   temp = temp%100;
   utemp = temp/10;
   stemp = temp%10;
Serial.print(temperatura);
Serial.print(" = ");
if (semn ==2) Serial.print("-");
else Serial.print("+");
Serial.print(ztemp);
Serial.print(utemp);
Serial.print(",");
Serial.print(stemp);
Serial.println(" ?");

HT1621_all_off(16);

  Write_1621(8,num[zora]);
  Write_1621(6,num[uora]);
  Write_1621(2,num[zmin]);
  Write_1621(0,num[umin]);

for (int i=0; i <= 3; i++)
{
  Write_1621(4,num[26]);  // -
  delay(1000);
  Write_1621(4,num[27]);  // empty space
  delay(1000);
}

   HT1621_all_off(16);
   delay(1000);

if (ztemp != 0)
{
if (semn == 2) Write_1621(10,num[26]); // -
  Write_1621(8,num[ztemp]);
}
else
if (semn == 2) Write_1621(8,num[26]); // -
  Write_1621(6,num[utemp]);
  Write_1621(4,num[stemp]+num[29]);  // number with decimal points
  Write_1621(2,num[28]);  // degree
  Write_1621(0,num[12]);  // C
  delay(3000);

}



void SendBit_1621(uchar sdata,uchar cnt)
{
  uchar i;
  for(i=0;i<cnt;i++)
  {
    WR0;
    if(sdata&0x80) DATA1;
    else DATA0;
    WR1;
    sdata<<=1;
  }
}

void SendCmd_1621(uchar command)
{
  CS0;
  SendBit_1621(0x80,4);
  SendBit_1621(command,8);
  CS1;
}

void Write_1621(uchar addr,uchar sdata)
{
  addr<<=2;
  CS0;
  SendBit_1621(0xa0,3);
  SendBit_1621(addr,6);
  SendBit_1621(sdata,8);
  CS1;
}

void HT1621_all_off(uchar num)
{
  uchar i;
  uchar addr=0;
  for(i=0;i<num;i++)
  {
    Write_1621(addr,0x00);
    addr+=2;
  }
}

void HT1621_all_on(uchar num)
{
  uchar i;
  uchar addr=0;
  for(i=0;i<num;i++)
  {
    Write_1621(addr,0xff);
    addr+=2;
  }
}

void Init_1621(void)
{
  SendCmd_1621(Sys_en);
  SendCmd_1621(RCosc);
  SendCmd_1621(ComMode);
  SendCmd_1621(LCD_on);
}
